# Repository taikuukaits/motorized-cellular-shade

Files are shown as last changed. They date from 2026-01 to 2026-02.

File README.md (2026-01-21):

# motorized-cellular-shade
Motorized cellular shades using ESPHome and cellular shade blinds from SelectBlinds.com

These blinds were among the cheapest (yet still nice) I could find for my blinds. They still ran me between $27 and $53 per shade.

This project uses the [Endstop Cover](https://esphome.io/components/cover/endstop/) of ESPHome.

# Getting Started

There are several steps needed to make your own shades. 

1. You will need to print the physical components from the `stl` directory
2. You will need to assemble the physical components using hardware from the `bom`
3. You will need to wire the electronic components
4. You will need to mount the shade and provide power
5. You will need to connect the shade to Home Assistant and ESPHome
6. You will need to provide the shade a YAML configuration file in `config`

This guide will only cover hardwiring the shades to 12V DC. Battery or solar is not currently supported. 

This will require Home Assistant with two add-ons, ESPHome and ESPHome Device Builder.
You will need to adopt the device into Home Assistant yourself.

# Electronics

The ESPHome code assumes the following wiring:
```
D1 to B-1A L9110
D2 to B-2A L9110
D6 to End Stop 1
D5 to End Stop 2
Both End Stops connect to GND.
```
NOTE: It's recommended that D6 represent UP or CLOSED or you will need to modify the YAML file.

This is recommended for power: 
```
5V on D1 mini to Buck Converter Out +
G on D1 mini to Buck Converter Out -
VCC on L9110 to Buck Converter In +
GND on L9110 to Buck Converter In -
Buck Converter In + to 12V Source
Buck Converter In - to 12V Source
```

# ESPHome

The complete YAML file is checked into source under examples, for a short explanation continue reading. This YAML was written with the help of AI.

Each of the two endstops are binary sensors in ESPHome
```
binary_sensor:
  - platform: gpio
    id: endstop_open
    name: "Endstop Open"
    pin:
      number: D6
      mode: INPUT_PULLUP
      inverted: true
    filters:
      - delayed_on: 20ms
      - delayed_off: 20ms

  - platform: gpio
    id: endstop_closed
    name: "Endstop Closed"
    pin:
      number: D5
      mode: INPUT_PULLUP
      inverted: true
    filters:
      - delayed_on: 20ms
      - delayed_off: 20ms
```
They are INPUT_PULLUP because we connect them to GND. They are inverted because when pressed they are shorted to GND (LOW when PRESSED)

The motor is driven by two switches:
```
switch:
  - platform: gpio
    id: motor_in1
    pin: D1
    restore_mode: ALWAYS_OFF

  - platform: gpio
    id: motor_in2
    pin: D2
    restore_mode: ALWAYS_OFF
```
These follow the [drivers table](https://docs.sunfounder.com/projects/3in1-kit-v2/en/latest/components/component_l9110_module.html) to control them, so HIGH on B1 and LOW on B2 sends the B motor in one direction and LOW on B1 and HIGH on B2 sends it in the other direction. LOW on both is stop.

The scripts control the motor, setting these pins as appropriate for the desired action. When we want the motor to open, one is high and the other low.
```
script:
  - id: motor_stop
    then:
      - switch.turn_off: motor_in1
      - switch.turn_off: motor_in2

  # OPEN direction
  - id: motor_open
    then:
      - script.execute: motor_stop
      - switch.turn_on: motor_in1
      - switch.turn_off: motor_in2

  # CLOSE direction
  - id: motor_close
    then:
      - script.execute: motor_stop
      - switch.turn_off: motor_in1
      - switch.turn_on: motor_in2
```

Finally, we leverage the end stop cover from ESPHome. This cover uses time to approximate how open or closed the shade is. And it invokes our script actions to control the motor and uses our endstops for sensing closing and open. 
```
cover:
  - platform: endstop
    name: "Endstop Cover"
    max_duration: 3min

    open_action:
      - switch.turn_on: open_cover_switch
    open_duration: 2min
    open_endstop: end_stop_open

    close_action:
      - switch.turn_on: close_cover_switch
    close_duration: 2min
    close_endstop: end_stop_closed

    stop_action:
      - switch.turn_off: open_cover_switch
      - switch.turn_off: close_cover_switch
```

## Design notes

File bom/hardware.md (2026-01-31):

Overall BOM

See notes for how these were calculated. These are not affiliate links; I am not affiliated with Amazon, AliExpress or any seller in any way.

Bearings and Rails 

| Component | Quantity | Unit Price | Link |
|---|---|---|---|
| Tr8x2 Lead Screw with Nut | 1 | 6.50 | [Amazon](https://www.amazon.com/dp/B08JLXKJKC)
| MR148-2RS Ball Bearings 8mm ID 14mm OD | 3 | 0.6795 | [Amazon] https://www.amazon.com/dp/B082PS75YB

Bolts,  Heat Set Inserts, Screws

| Component | Quantity | Unit Price | Link |
|---|---|---|---|
| M2.5 Socket 6mm | 4 | 0.05 | [Amazon](https://www.amazon.com/dp/B07PS8V4V3)
| M2.5 Heat Insert, Length 3mm, OD3.5 | ? | $0.04 | [Amazon](https://www.amazon.com/dp/B0B47MZ1SG) |
| M2.5 Grub Screw 5mm | ? | $0.05 | [AliExpress](https://www.aliexpress.us/item/2251832749671024.html) |
| M2.5 Countersunk 8mm | ? | 0.07 | [Amazon](https://www.amazon.com/dp/B0B88STRPX)

| M3 8mm Socket | 4 | 0.05 | [Amazon](https://www.amazon.com/dp/B07PS8V4V3)
| M3 Heat Insert, Length 3mm, OD5 | ? | $0.04 | [Amazon](https://www.amazon.com/dp/B0B47MZ1SG) |

| M2 Socket 12mm | ? | 0.07 | [Amazon](https://www.amazon.com/dp/B0B88STRPX)
| M2 Nuts | 4 | 0.05 | [Amazon](https://www.amazon.com/dp/B07PS8V4V3)

Per Component
 - - Motor Holder (Each)
 -     - (2x) M2.5 insert - 3.5mm O.D - 3mm long
 -     - (2x) M2.5 grub screw - 5mm long
 - - End Stop Holders (Each)
 -     - (2x) M2.5 insert - 3.5mm O.D - 3mm long
 -     - (2x) M2.5 grub screw - 5mm long
 -     - (2x) M2 12mm bolts
 -     - (2x) M2 nuts

 The inserts to the Shaft are all OD 3
 (motor shaft coupler and rope holders)
 The inserts to hold the boxes in place are all 3.2

 - - Electronics Stack
 -     - Bottom
 -         - Heat Inserts
 -             - (6x) M2.5 insert - 3.5mm O.D - 3mm long
 -         - To Attach the Board
 -             - (4x) M2.5 bolt - 'socket' head - 6mm long
 -     - Middle
 -         - To Attach to Bottom board
 -             - (2x) M2.5 bolts - 'socket' head - 6mm long
 -         - Heat Set Inserts
 -             - (4x) M2.5 insert - 3.5mm O.D - 3mm long
 -     - Top
 -         - To Attach to the Middle Board
 -             - (4x) M2.5 bolts - 'socket' head - 6mm long
 - Totals: 10x Heat Set Inserts 2.5x3.5x3, 10x M2.5 Socket 6mm long

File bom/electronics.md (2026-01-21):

I used the following. These are not affiliate links; I am not affiliated with Amazon, AliExpress or any seller in any way.

| Component | Quantity | Unit Price | Link |
|---|---|---|---|
| D1 Mini | 1 | $3.00 | [Amazon](https://www.amazon.com/dp/B081PX9YFV) |
| Mini360 Buck Converter | 1 | $0.89 | [Amazon](https://www.amazon.com/dp/B07T7L51ZW) |
| L9110S | 1 | $1.44 | [Amazon](https://www.amazon.com/dp/B0923VMKSZ)
| Micro Switch | 2 | $0.25 | [Amazon] (https://www.amazon.com/dp/B07YKH3TDR) 
| 20GA180 Motor (12V 30 RPM) | 1 | $4.22 | [AliExpress] (https://www.aliexpress.us/item/2255800587435465.html)

The motor is the most expensive and I had to order them in bulk. I ended up ordering 14 at unit price of 3.05 but the total with shipping was 59.04. They are much more expensive on Amazon and eBay.

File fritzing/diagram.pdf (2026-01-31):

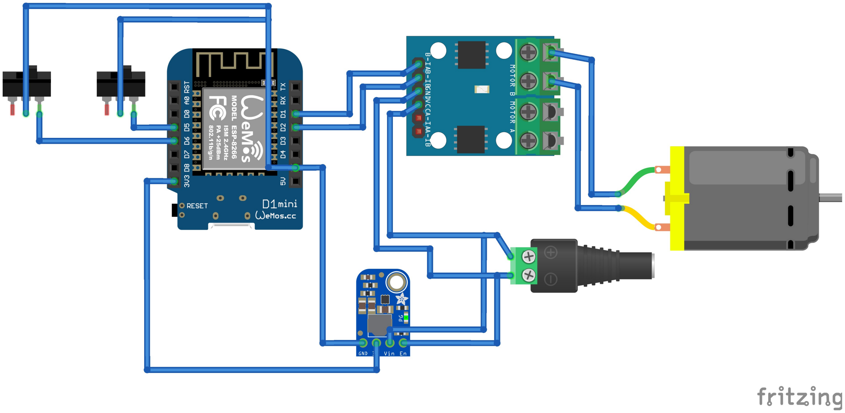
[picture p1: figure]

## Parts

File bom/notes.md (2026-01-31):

I've tried to reduce the number of components, preferring M2.5 fasteners and M2.5 heat inserts (and grub screws).
That said, the end stop mounting holes are too small for 2.5 so they use M2 bolts and M2 nuts
The Lead Screw holes are too large so they use M3 bolts and heat sets. It can't use nuts due to clearance. If your lead screw holes are threaded you don't need M3 heat sets. Theoretically you could buy Tr8x2 nuts with M3 threads but at ~1.5 per lead screw its not worth it since heat sets are cheap (~6.5 for 100 = 25 blinds, or 37.5 in nuts)
Lastly the motor although it uses M2.5 it needs a counter sink screw. The rest are bolts. 

Also generally I found it cheaper to buy assortments; ie buying an M2 assortment got you 20 12mm M2 screws and 200 nuts for 6.59 but buying 100 12mm M2 might cost 5.99. So if you are building less than 5 blinds, the assortment makes sense. You will pay more on Amazon vs AliExpress but AliExpress is way cheaper; for example you can get the same M2 12mm 50pcs for 2.24 shipped (or 1 on sale). So if you are willig to wait you can spend significantly less. For some items, even McMaster can be cheapest - M2 100 pcs 12mm are 4.46 but you will need to pay shipping.

Hardware I used the price I paid. If I paid shipping, its included. You might be able to save by finding alternate suppliers. 

In some cases I used assortments. When I used an assortment I took cost divided by the total number which is not really accurate. If you need to build 10 of these at 1 screw each and the assortment has 9 screws you are going to need two assortments even if thats the only screw you needed 10. This could artificially inflate the cost of my fasteners. 

When buying a lead screw, make sure you get Tr8x2 because we want maximum rotations for minimum travel distance of the lead screw. If you get a T8x8 for example you will likely exceed the avaiable space in the shade while trying to roll it up. 

I found Amazon cheapest for lead screws but did look at bulkman3d for 1.99 a lead screw but really high ($80) shipping. At some point it would make sense. I needed around 13 so its close at 145.12 but Amazon was still cheaper at 120.93 for all. 

For heat set insert sizing, best I could find was prusa: https://www.prusa3d.com/product/heat-set-inserts-m2-5-standard-100-pcs/

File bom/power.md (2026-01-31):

Power was trickier, these are things I considered useful, nothing is really required, you just need a 12V source per shade.

These are not affiliate links; I am not affiliated with Amazon, AliExpress or any seller in any way.

Power jacks for the first blind in a series: https://www.amazon.com/gp/product/B07Y2W997D
Slim power jacks to run on the wall: https://www.amazon.com/dp/B081CTBVF5
12V 3A power adaptor with barrel plug: https://www.amazon.com/Facmogu-Transformers-Connector-5-5x2-5mm-5-5x2-1mm/dp/B0CQ7M3MM1

This is the only one I didn't personally order but I thought I did and probably will:
Flat Wire: https://www.amazon.com/FRANKEVER-Adhesive-Conductor-Electrical-Connectors/dp/B07K84MTLC/

These were only useful for prototyping IMO but I did like them though they could be unreliable:
Quick Splice: https://www.aliexpress.us/item/3256803191481429.html

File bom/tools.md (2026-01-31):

Heat set insert tips (24.95): https://www.amazon.com/dp/B08B17VQLD

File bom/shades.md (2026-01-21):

I sourced my shades from selectblinds.com all of this variety: https://www.selectblinds.com/cellular-shades/light-filtering-cordless-cellular-shades.html?ColorId=9003. These are not affiliate links; I am not affiliated with selectblinds or any seller in any way.

Shades purchased:
- 2022: 27.81 each: 16 1/2" w x 30 1/4" h
- 2020: 37.88 each: 20 7/8" w x 50" h
- 2020: 53.27 each:  16 1/4" w x 61" h
- 2020: 29.075 each: 16 1/2" w x 30 1/4" h

These were calculated by taking the order total after discounts and shipping and dividing by number of blinds ordered.

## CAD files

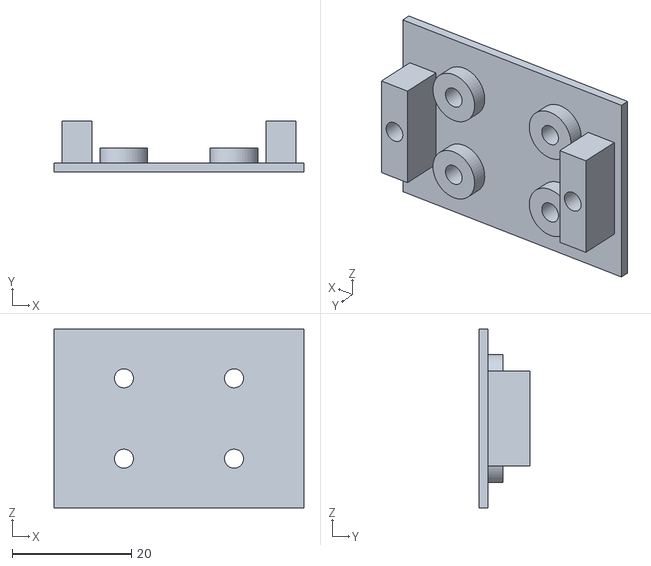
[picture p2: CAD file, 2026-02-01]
stl/Blind Electronics Stack Bottom V1.0.3.stl
42.0 x 8.50 x 30.0

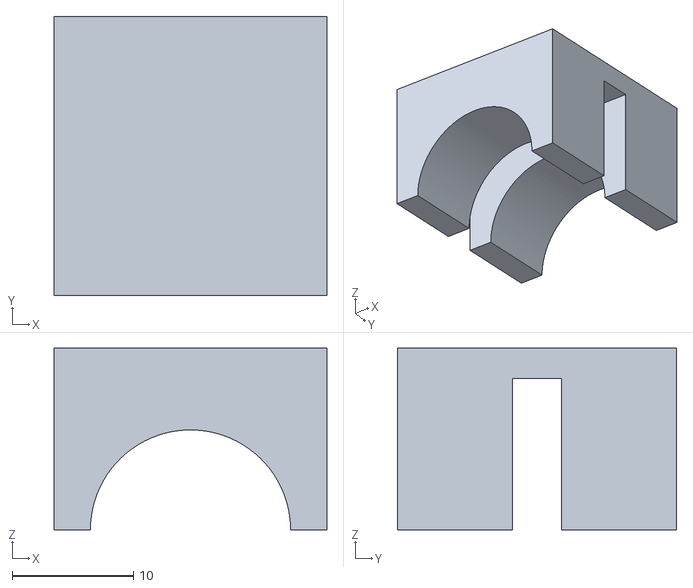
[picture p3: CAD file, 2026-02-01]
stl/Setup Inset Block - Rope Holder V1.0.1.stl
22.5 x 23.0 x 15.0

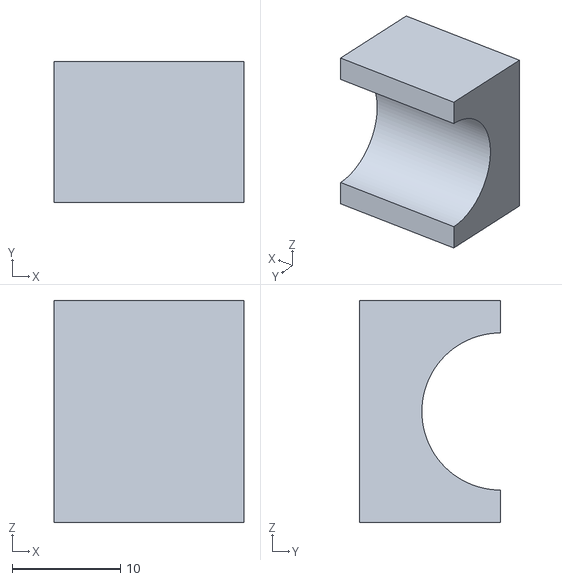
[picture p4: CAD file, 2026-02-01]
stl/Setup Inset Block - Shaft Bearing V1.0.0.stl
17.5 x 13.0 x 20.5

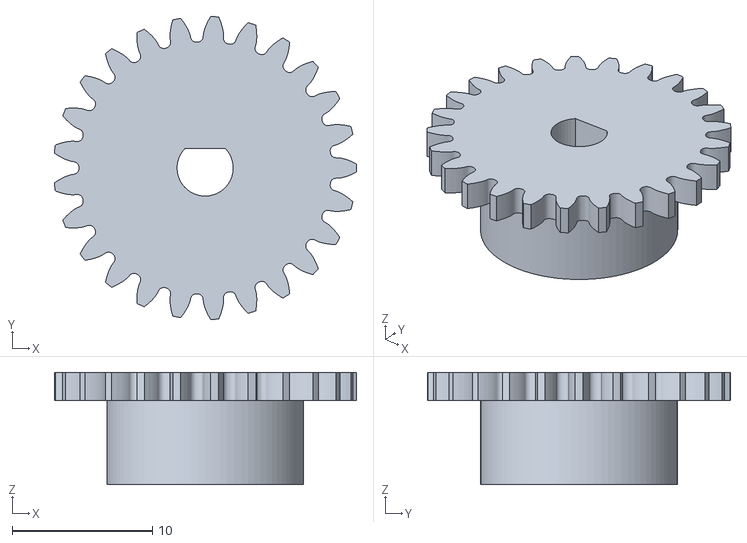
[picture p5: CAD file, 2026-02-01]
stl/Motor Gear V1.0.3.stl
21.5 x 21.6 x 8.00

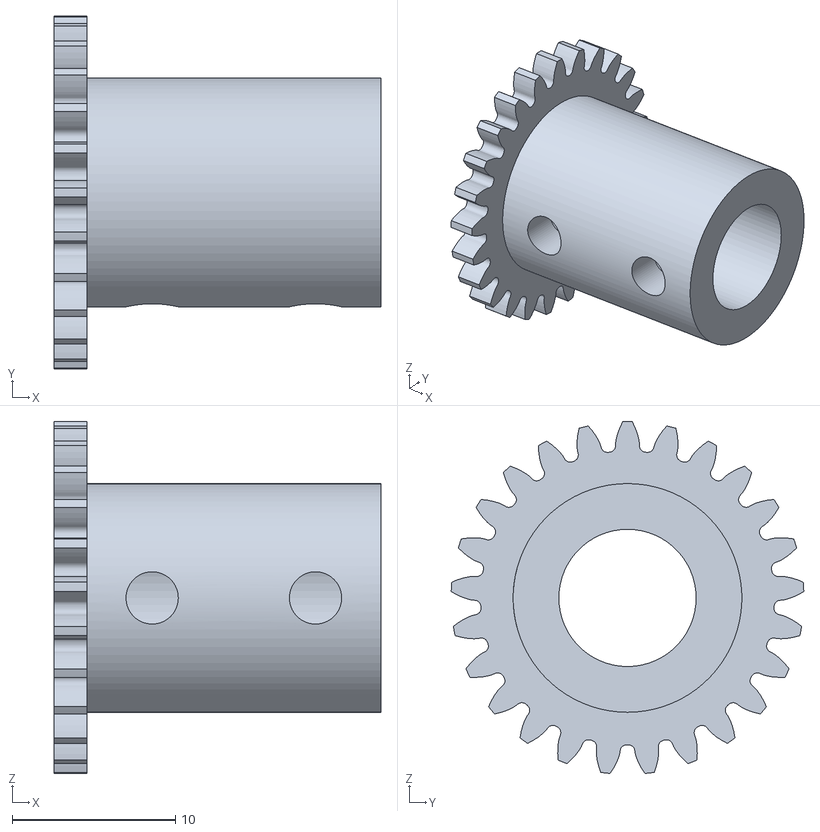
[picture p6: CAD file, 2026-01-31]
stl/Shaft Motor Gear V1.0.1.stl
20.0 x 21.6 x 21.5

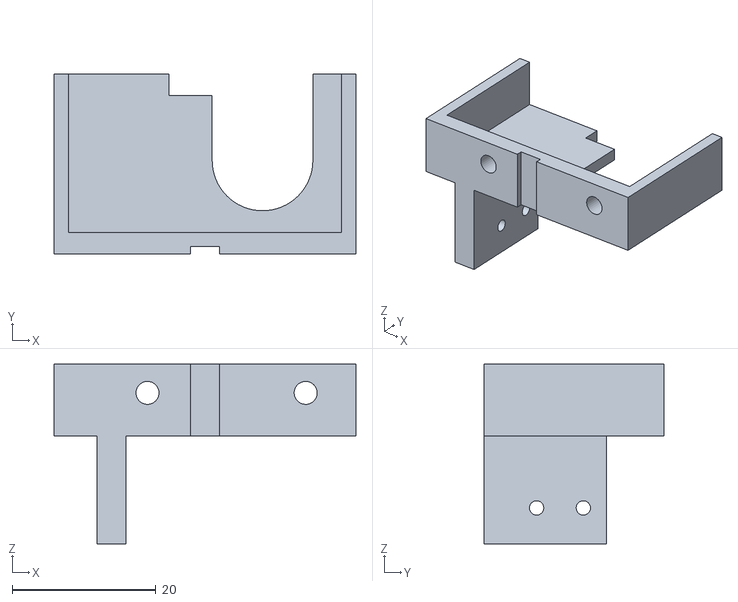
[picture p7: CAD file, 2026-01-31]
stl/End Stop Holder V1.0.2.stl
42.0 x 25.0 x 25.0

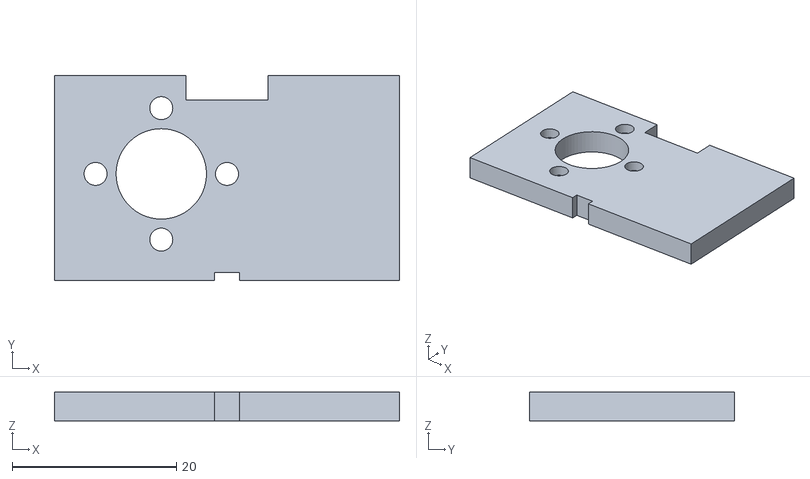
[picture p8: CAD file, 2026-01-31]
stl/Lead Block Barrier V1.0.2.stl
42.0 x 25.0 x 3.50

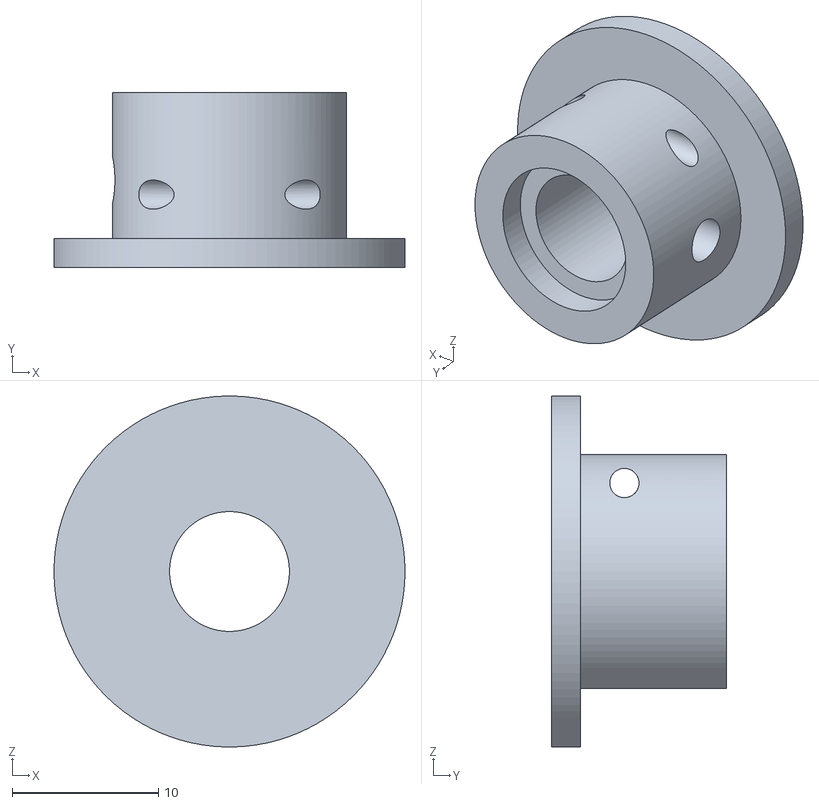
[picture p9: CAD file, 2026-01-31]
stl/Rope Holder Bottom V1.0.1.stl
24.0 x 12.0 x 24.0

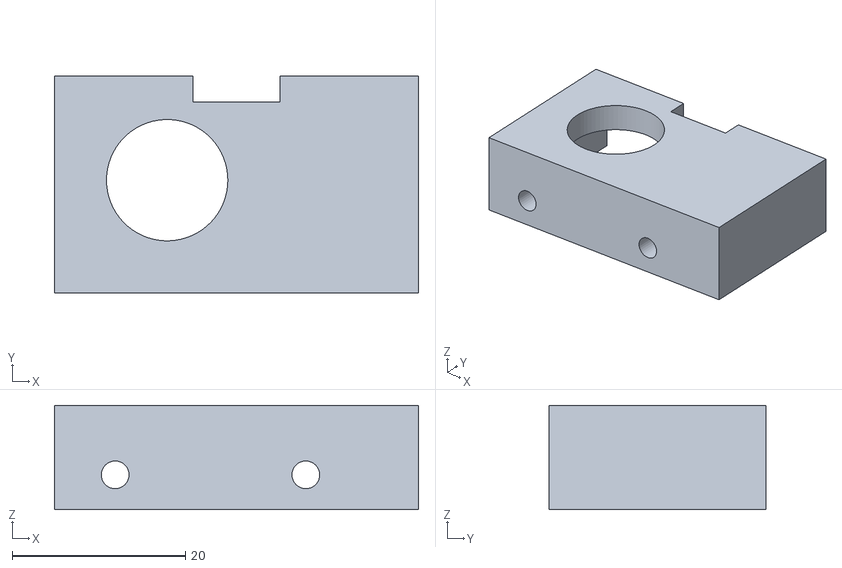
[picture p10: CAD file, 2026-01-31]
stl/Shaft Bearing Holder V1.0.2.stl
42.0 x 25.0 x 12.0

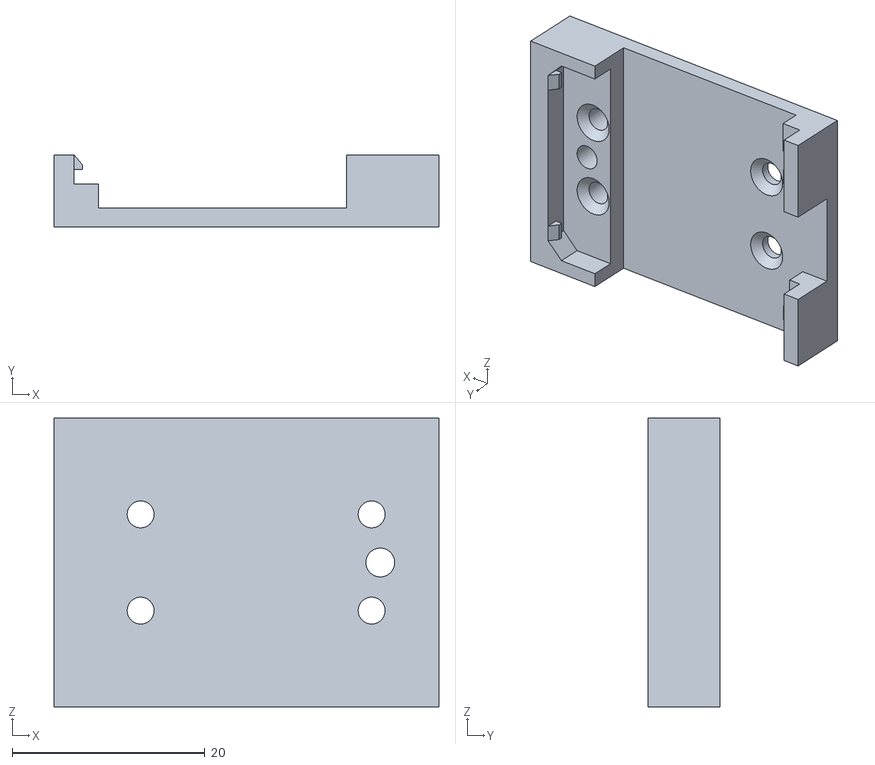
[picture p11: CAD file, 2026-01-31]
stl/Blind Electronics Stack Top V1.0.2.stl
40.0 x 7.50 x 30.0

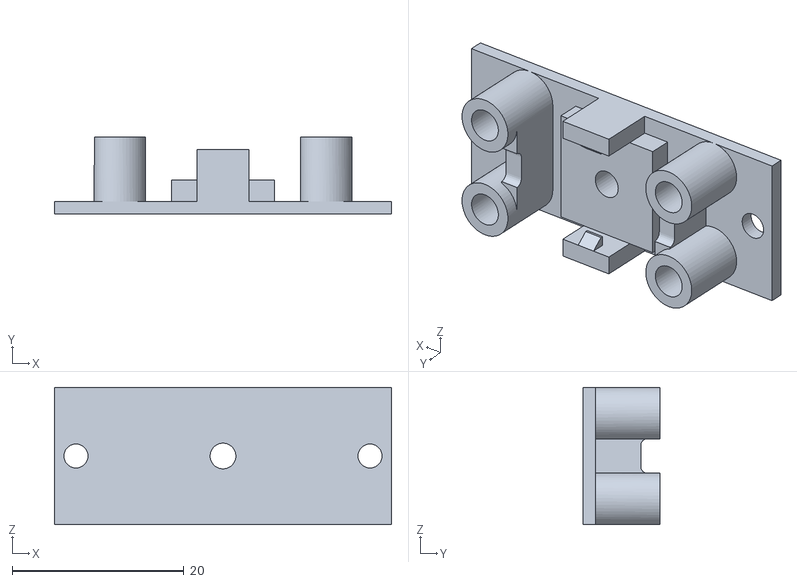
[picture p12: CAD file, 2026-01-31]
stl/Blind Electronics Stack Middle V1.0.1.stl
39.2 x 9.00 x 16.0

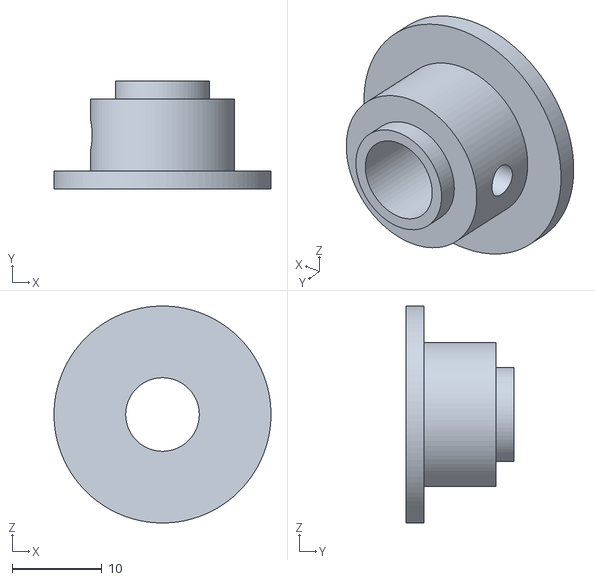
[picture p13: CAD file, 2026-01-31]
stl/Rope Holder Top V1.0.1.stl
24.2 x 12.0 x 24.2

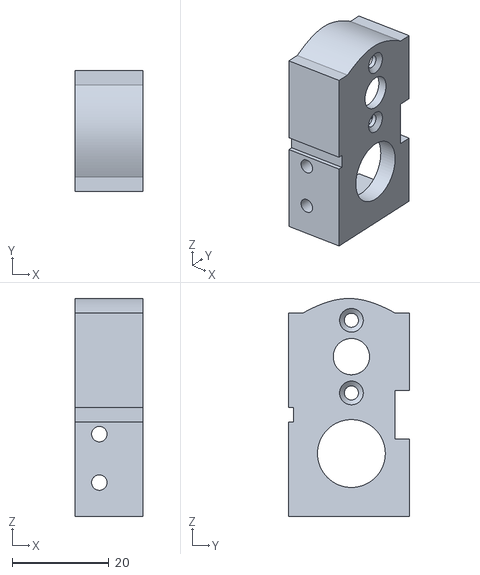
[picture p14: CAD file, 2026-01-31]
stl/Motor Holder V1.0.1.stl
14.0 x 25.0 x 45.0

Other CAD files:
stl/End Stop Holder V1.0.2 Mirror.stl
stl/Shaft Bearing Holder V1.0.2 Mirror.stl

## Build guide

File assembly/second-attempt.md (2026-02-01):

Largely went well. Big issue was getting the motor gear on. It deformed it. I added a small cutout for the motor to hopefully align it. Other than that assembly went well. The order is still important even though I made it a little reduced. 

Final alignment is annoying/tricky but not too bad. Also getting some twisting.

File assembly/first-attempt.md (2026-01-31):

1/28/2026 tried to assemble the first "production" blind (IE blind that will operate in my house).

Some notable issues, which required STL changes; and BOM changes. 

6mm grub screws is way too long, I thought they would feed out the back. 3mm is fine thats the length of my inserts.

Extra plastic behind inserts can melt and get in the way. 

Press is needed for motor gear. 

1/29/2026: 

Getting the rope UNDER the parts is difficult,  a small channel would help. 
The tops of the pieces being closed means you need to assemble everything then slide it in. 
Modified the end stop to be open so they can be placed in any order.
Added rope reliefs to things that needed it. 

Other than that assembly was completed. Saying it went smooth feels like a bit of a stretch. 
I did things 'backward' IE the motor orientation drives everything. 
And then even knowing that I still flipped it.

Then actually getting the pieces into the blind was a bit of an annoying thing. 
Some of the set screws were too far and made it difficult to insert into the blind. 
Then some of the unset set screws (motor) had plastic preventing me from putting the screw in. 

Ultimately I completed my goal but it was a bit of a slog.

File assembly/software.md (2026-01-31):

(Recommend doing this on a PC with WiFi)

Navigate to Home Assistant: http://homeassistant.local:8123/
Add On: ESPHome Device Builder
Open Web UI
Click "New Device"
Click "Continue"
Click "Empty Configuration"
Name it something ie, "Bay Window 5"
Click "Edit" on newly created device. 
Copy/paste motorized-shade.yaml (but replace with your REDACTED fields or copy/paste from existing shade)
Remember to replace name and friendly name with your devices. 
Then click install. 
Select "manual download".
Save file when completed. 

Navigate to "https://web.esphome.io/"
Click "Install" 
Choose file: pick file downloaded
Click "Install" 

Wait for 100%: Configuration installed!

Unplug device (turn off power) and plug back in. Should appear ONLINE in ESPHome.

Now you should be able to deploy directly from ESPHome and should see the device in Home Assistant.

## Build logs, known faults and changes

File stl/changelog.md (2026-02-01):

- Jan 31 2026
Added supports for doing the 3d inserts on round parts. Tried to make motor alignment easier. 

Actually difficult here to get the ropes in alignment. Not sure why the first was so easy. 
I think the key is to do the ropes BEFORE you solder the motor so you can easily move it. 

- Jan 29 2026

Biggest current assembly pains: End Stops must be inserted in order. Have to get boxes over the rope but are too precisely sized. 

End Stop Holder: Removed lead screw capture. Added rope relief.
Motor Holder: Added rope relief. Moved one insert to make room for relief.
Lead Block Barrier: Added rope relief. 

-  Jan 28 2026

Boxed End Stop 1.0.2: Shrank the 'foot' to make more room for the grub screw and insert. While inserting an heat set insert it 'clogged up'. I think just lowering the amount of excess plastic should solve this.

Shaft Bearing Holder V1.0.1: Same clogging, lowered foot by 1mm. Also recommend to print a mirrored one. 

Lead Block Barrier 1.0.1: Switched to M2.5 and nuts. The M3 screws while they have no slack, their inserts are just too close to the edge. Heat sets are too risky this close to the edge. M2.5 with nuts is a pretty tight fit, but also slack (backlash) is not really a problem (even if there was a lot) due to the endstop design. This also eliminates M3 from the equation. 

Top Electronic Stack 1.0.2: didnt quite have proper clearance for D1 mini. Using countersunk screws here (already in the motor) because of clearance issues with the USB port (and it looks nicer).

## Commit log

2022-03-25 feat: adding example script to drive motors.
2022-03-28 feat: Calibration using MQTT messages instead of home assistant numbers.
2022-03-28 feat: Added a shade-boss script to help with calibration.
2022-03-28 feat: Working eeprom and position calibration.
2023-01-22 feat: Implemented the first pass of new motor.
2023-01-22 refactor: Moving motor code into the original motor driver class.
2023-01-31 refactor: Tightening up the code, moving multiline prints to dedicated log file, printing closed position/
2023-03-25 doc: Adding BOM for electronics stack.
2023-03-25 doc: Bottom stack uses M2.5 instead of M3 to attach the board. Added 3d models for electronics stack.
    [Blind Electronics Stack Bottom.3mf, Blind Electronics Stack Bottom.stl, Blind Electronics Stack Middle.3mf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]
2026-01-21 purging irrelevant files
    [Blind Electronics Stack Bottom.3mf, Blind Electronics Stack Bottom.stl, Blind Electronics Stack Middle.3mf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]
2026-01-21 adding model files V1.0.0
    [Blind Electronics Stack Bottom V1.0.0.stl, Blind Electronics Stack Middle V1.0.0.stl, Blind Electronics Stack Top V1.0.0.stl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]
2026-01-21 example yaml file
    [motorized-shade.yaml]
2026-01-21 Revise shade assembly instructions in README
    Updated instructions for building shades, including printing and assembling components, and connecting to Home Assistant.
2026-01-21 adding bom entries for most things
    [motorized-shade.yaml]
2026-01-21 more bom
2026-01-22 added motor holder
    [End Stop Holder V1.0.0.stl, Motor Holder V1.0.0.stl]
2026-01-31 reduced bom. new mirrored versions. added slots for rope and wires.
    [Blind Electronics Stack Bottom V1.0.0.stl, Blind Electronics Stack Bottom V1.0.1.3mf, Blind Electronics Stack Bottom V1.0.1.stl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]
2026-02-01 setup blocks,
    [Motor Gear V1.0.1.stl, Motor Gear V1.0.2.stl, Motor Gear V1.0.3.stl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]
2026-02-01 removing old stls
    [Blind Electronics Stack Bottom V1.0.1.stl, Blind Electronics Stack Bottom V1.0.3mf, Blind Electronics Stack Top V1.0.1.stl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]
2026-02-01 fix stl file
    [Blind Electronics Stack Bottom V1.0.3.stl, Blind Electronics Stack Bottom V1.0.3mf]
